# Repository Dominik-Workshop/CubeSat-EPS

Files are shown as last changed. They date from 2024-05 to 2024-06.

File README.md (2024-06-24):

# EPS - Electric Power System

## Used tools:
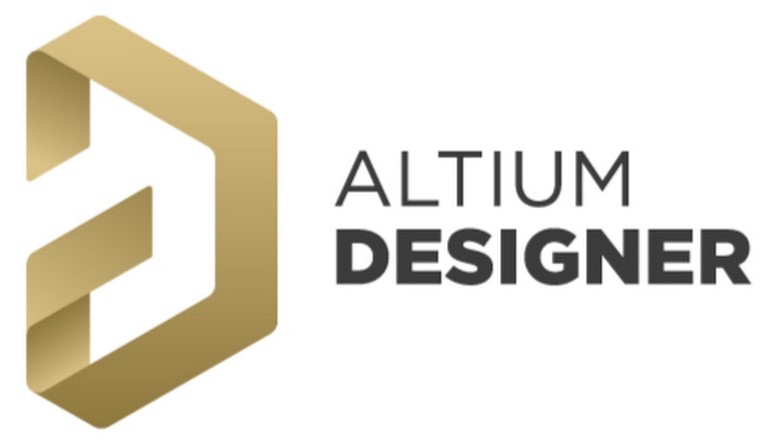
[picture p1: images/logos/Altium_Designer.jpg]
&nbsp;&nbsp;&nbsp;&nbsp; &nbsp;&nbsp;&nbsp;&nbsp; 
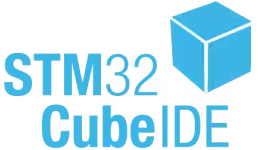
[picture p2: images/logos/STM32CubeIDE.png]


# Project Overview
This project is part of a CubeSat prototype built as a group project at Wrocław University of Science and Technology. [GitLab Repository](https://gitlab.com/wust-satellite)
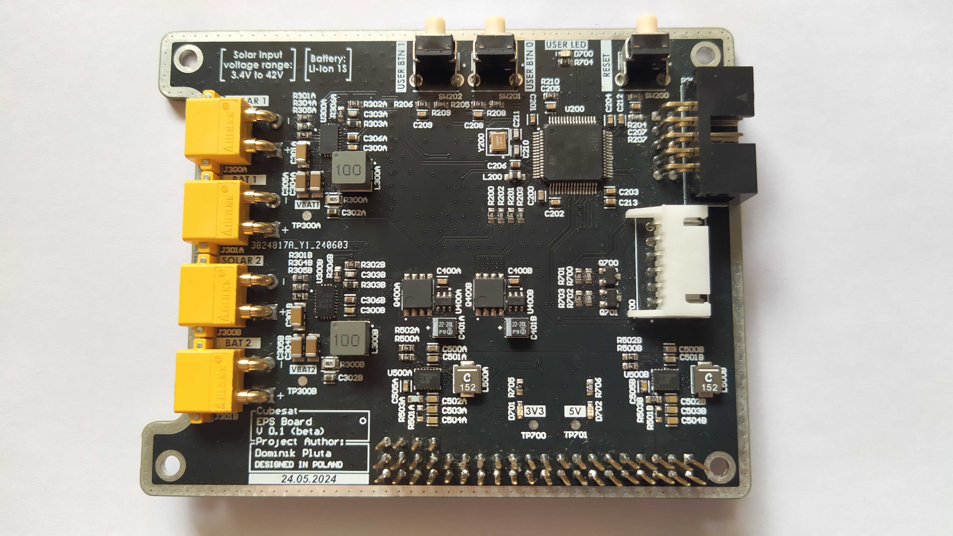
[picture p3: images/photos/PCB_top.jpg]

The primary functions of this board are:

1. **Battery Management**:
    - Charging a 1S Li-ion battery pack using Maximum Power Point Tracking (MPPT).
    - Monitoring the battery voltage.

2. **Power Conversion**:
    - Generating stable 5V and 3.3V power rails to supply various components of the system.

3. **Communication**:
    - Establishing UART communication with a radio board for data transmission and control.

4. **Deployment of Solar Panels and Radio Antenna**:
    - Providing two power outputs capable of driving high current to external resistors, which can burn wires to deploy the solar panels and antenna.

5. **Remove Before Flight (RBF) Circuit**:
    - Ensuring that the satellite starts operation only after ejection from the launch vehicle.

> [!NOTE]
> Certain features, such as current monitoring and switches on all power lines, were omitted due to time constraints.

# Schematic - top sheet
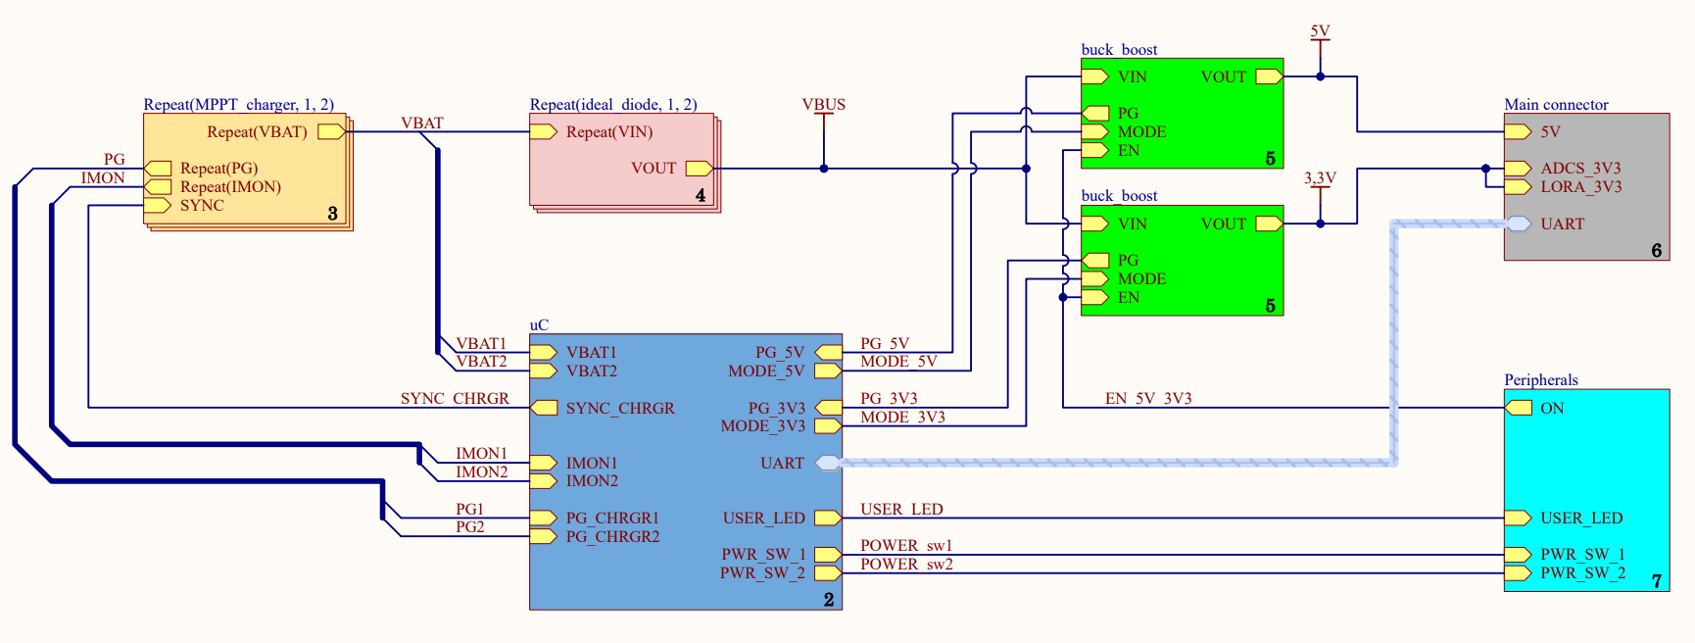
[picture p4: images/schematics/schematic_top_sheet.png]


# PCB
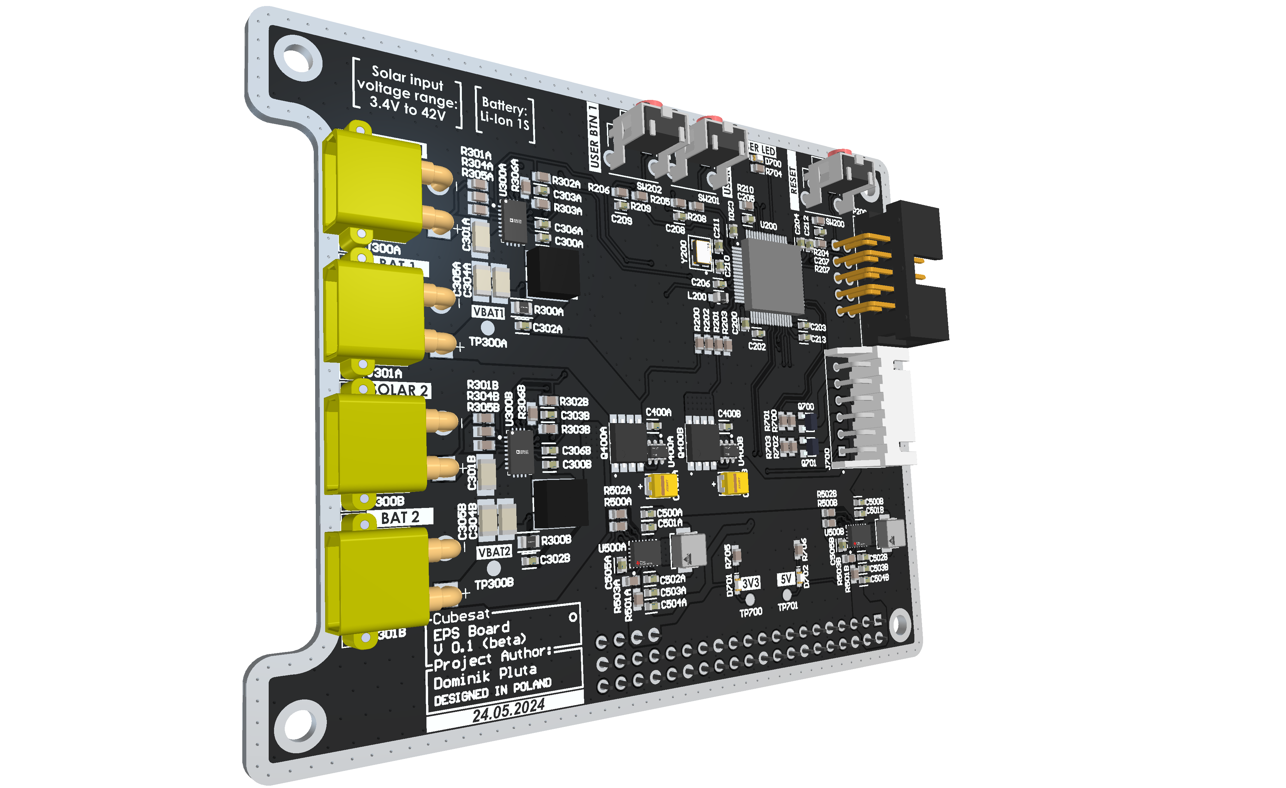
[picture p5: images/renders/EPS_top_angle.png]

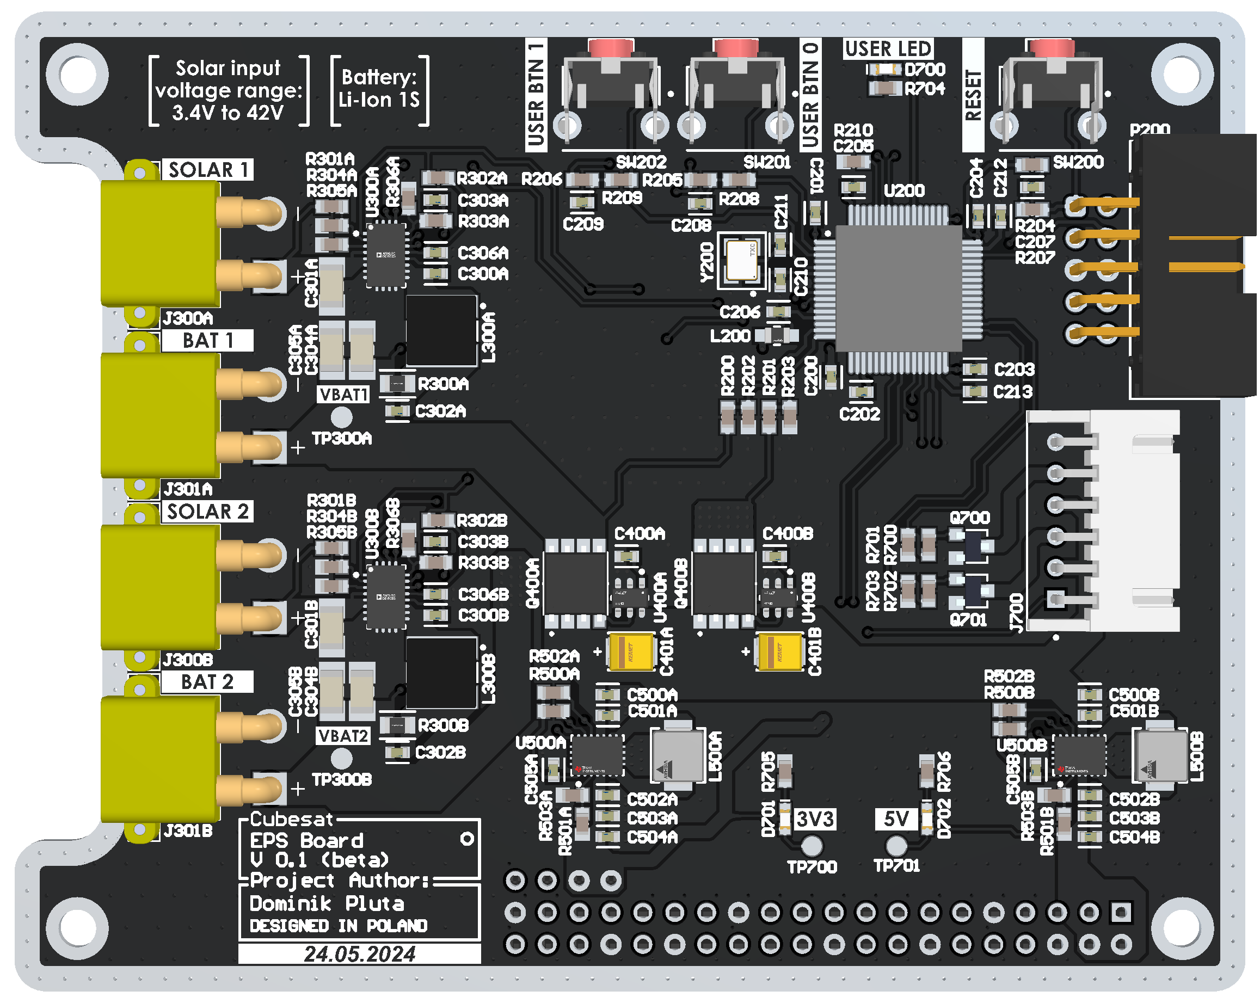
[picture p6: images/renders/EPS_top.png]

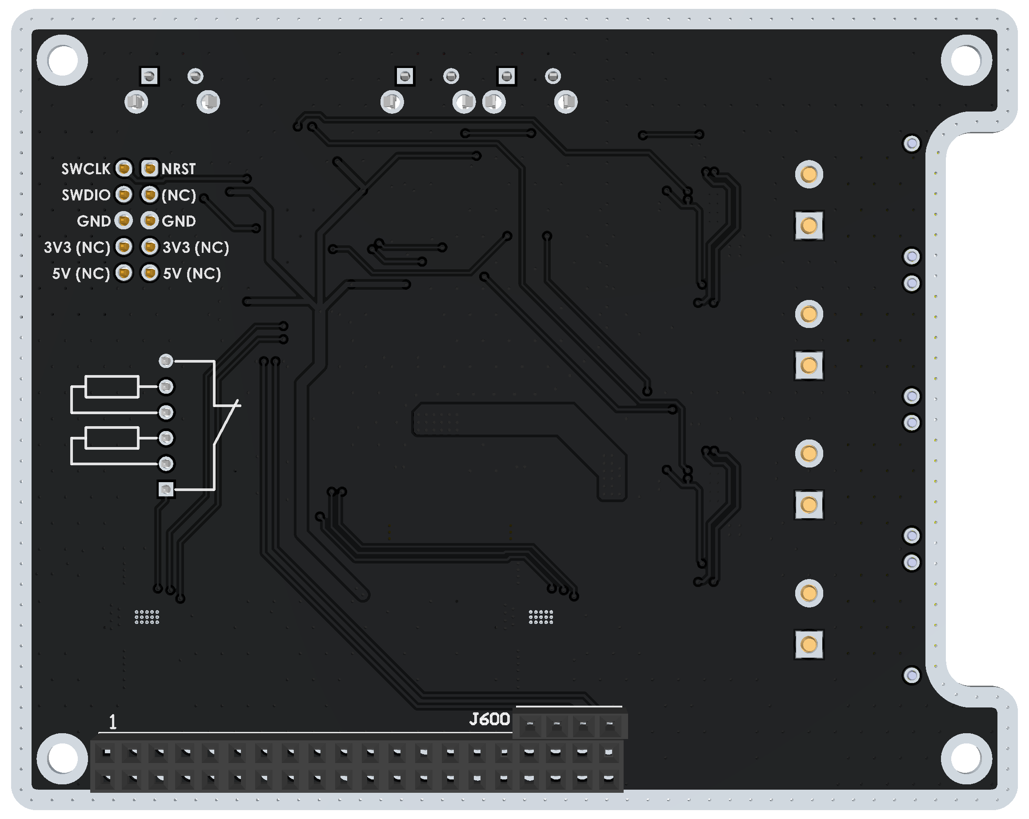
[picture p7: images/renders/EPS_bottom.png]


# Project structure
```
.
├── images
│   ├── logos
│   ├── photos
│   ├── renders
│   └── schematics
├── pcb
│   ├── ***Altium schematic and PCB Documents***
│   ├── ***Altium CAMtastic Documents***
│   ├── ***other Altium files***
│   ├── Lib
│   │   └── ***My parts libraries***
│   └── Project Outputs for EPS_board
│       ├── EPS_full_schematic.pdf
│       ├── ***Gerber and NC drill files***
│       └── EPS_gerber_files.zip
├── code
│   └── ***STM32CubeIDE project***
└── README.md
```

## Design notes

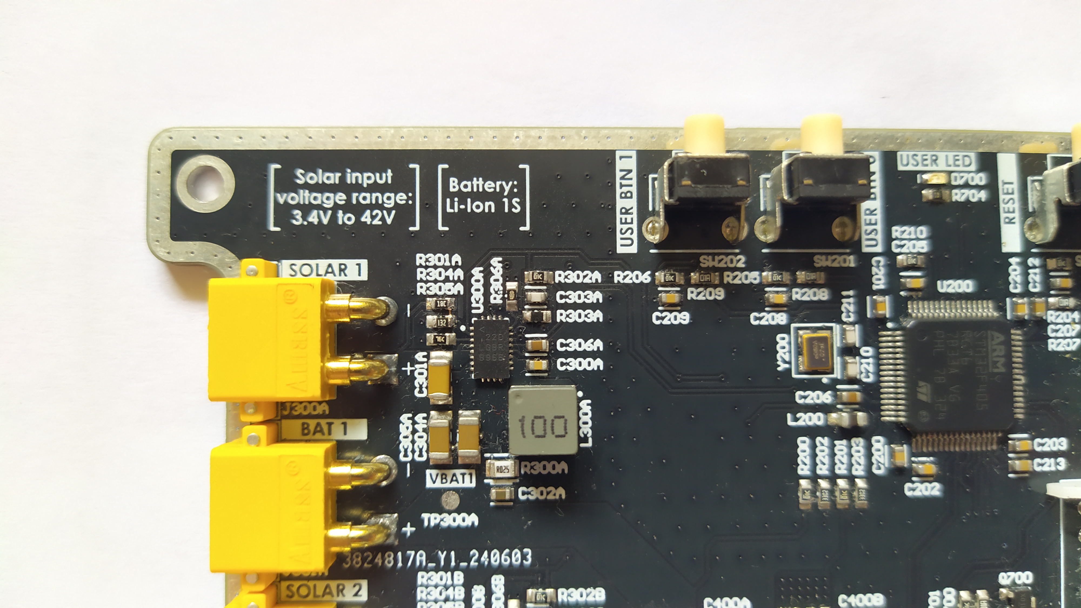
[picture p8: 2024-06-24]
images/photos/PCB_top_closeup2.jpg

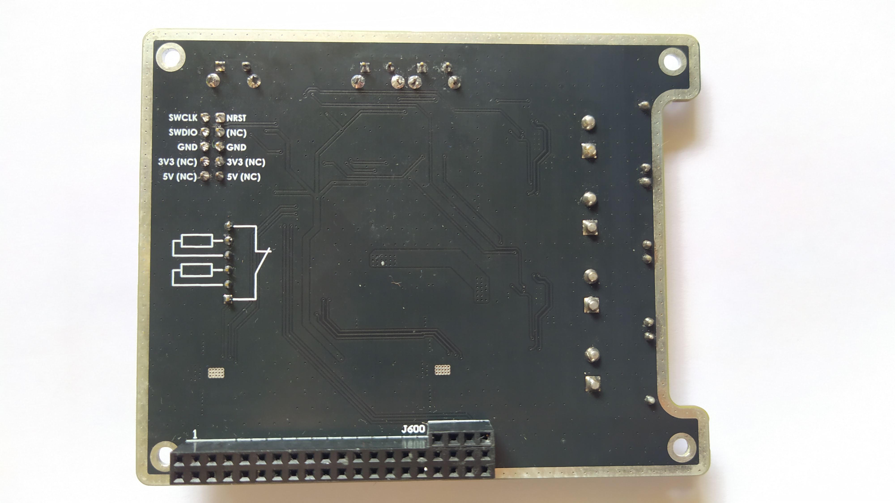
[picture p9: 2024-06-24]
images/photos/PCB_back.jpg

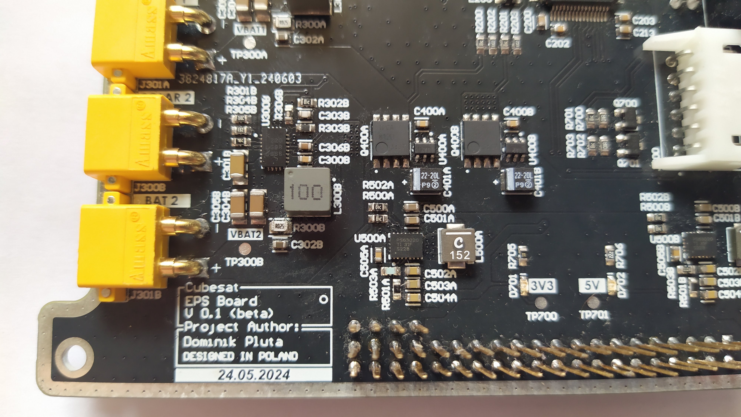
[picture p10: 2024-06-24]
images/photos/PCB_top_closeup1.jpg

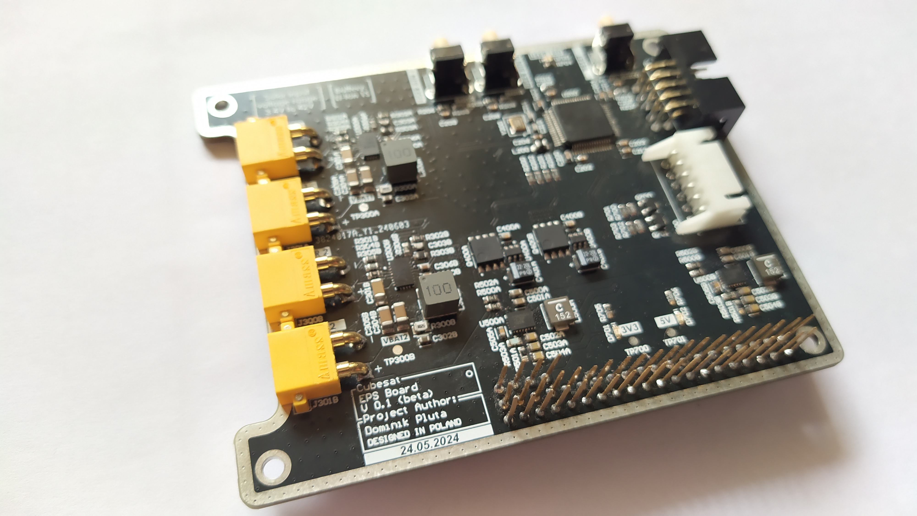
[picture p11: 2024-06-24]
images/photos/PCB_top_angle.jpg

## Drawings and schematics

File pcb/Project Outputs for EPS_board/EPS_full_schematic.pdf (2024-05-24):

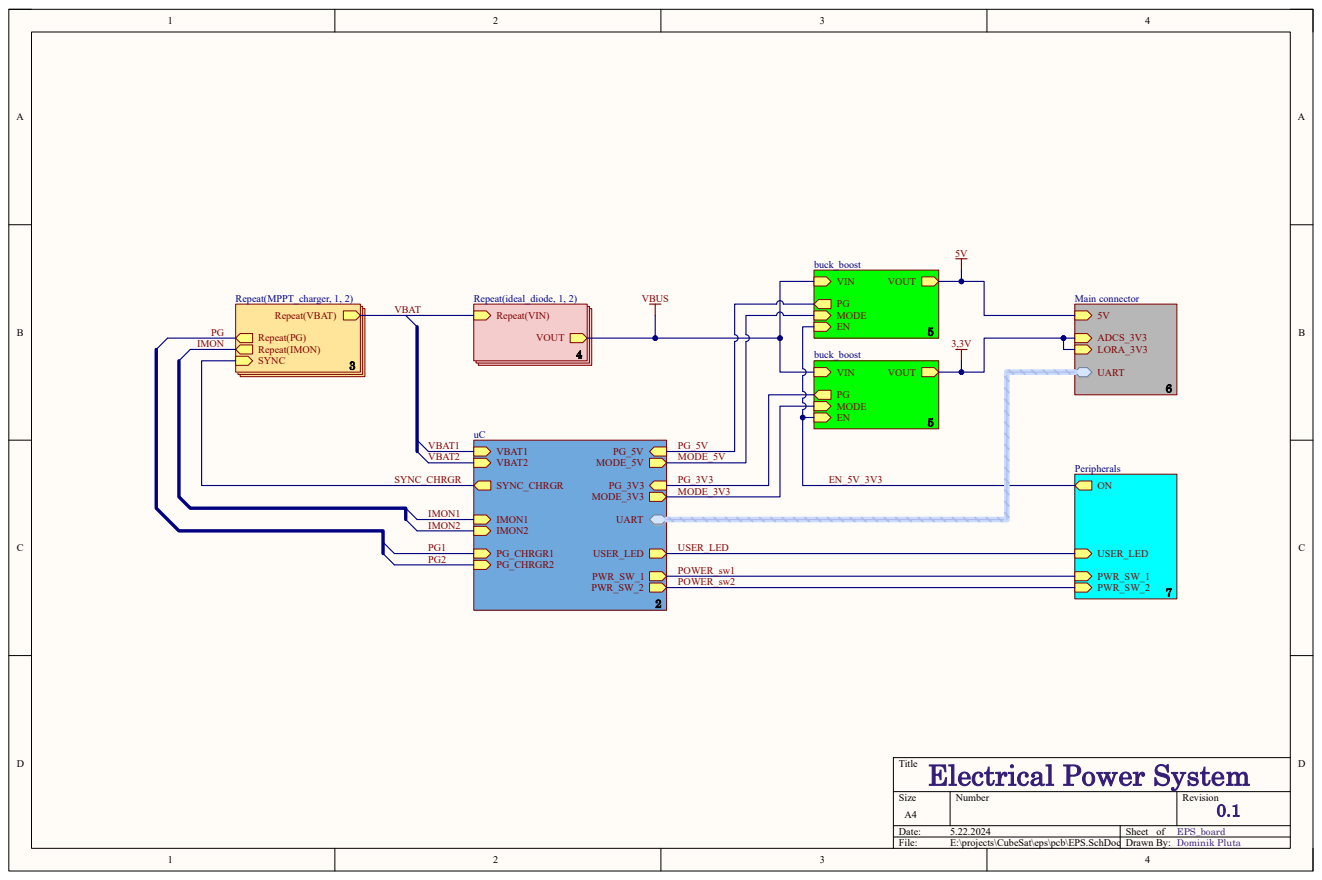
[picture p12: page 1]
Size; Number; Revision; Date:; Sheet of; File:; E:\projects\CubeSat\eps\pcb\EPS.SchDoc; Drawn By:; VBAT1 VBAT2; USER_LED; MODE_5V; MODE_3V3; IMON1; PG_CHRGR1; SYNC_CHRGR; IMON2; PG_CHRGR2; UART; PWR_SW_1 PWR_SW_2; Repeat(PG) Repeat(IMON); Repeat(VBAT); SYNC; Repeat(MPPT_charger, 1, 2); Dominik Pluta; EPS_board; VIN; MODE; VOUT; buck_boost; 3,3V VOUT; Repeat(VIN); Repeat(ideal_diode, 1, 2); VBAT; ADCS_3V3 LORA_3V3; Main connector; Peripherals; VBUS; PG_3V3 MODE_3V3; PG_5V MODE_5V; IMON1 IMON2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

Electrical Power System
Title

# uC power supply Voltage divider

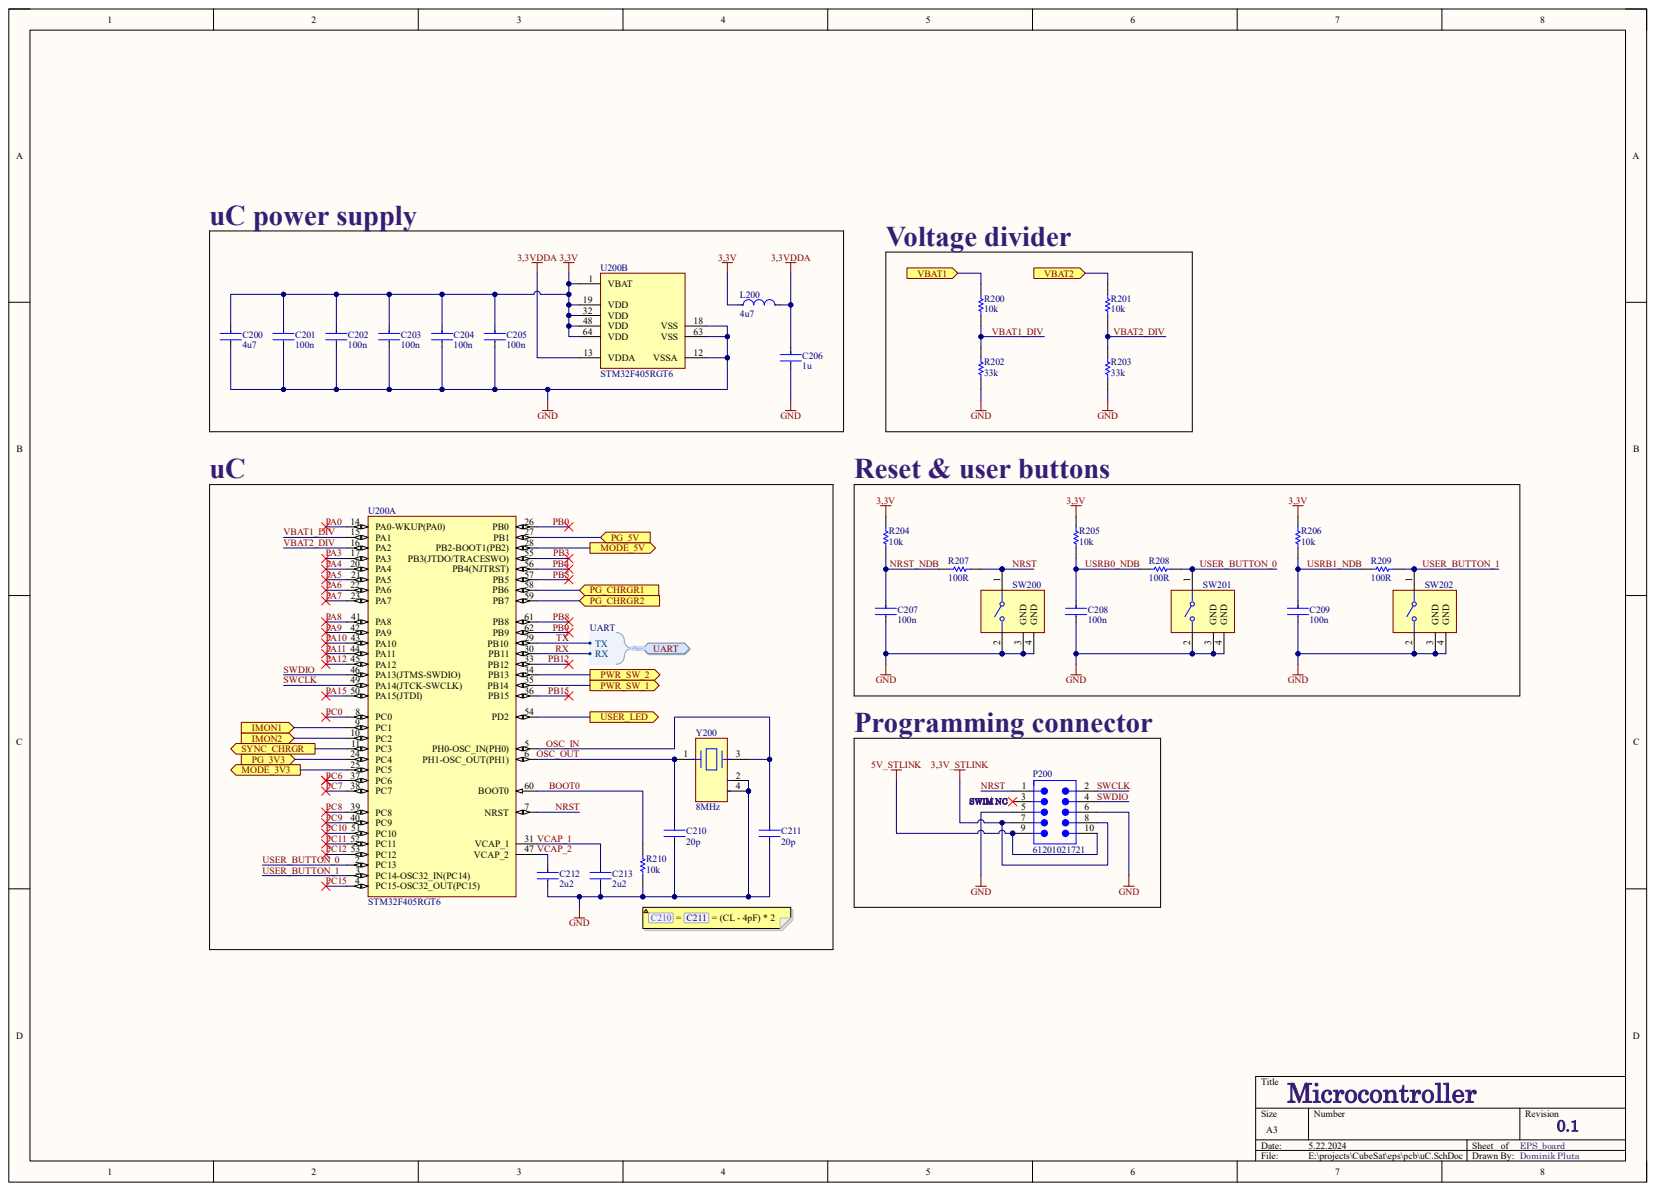
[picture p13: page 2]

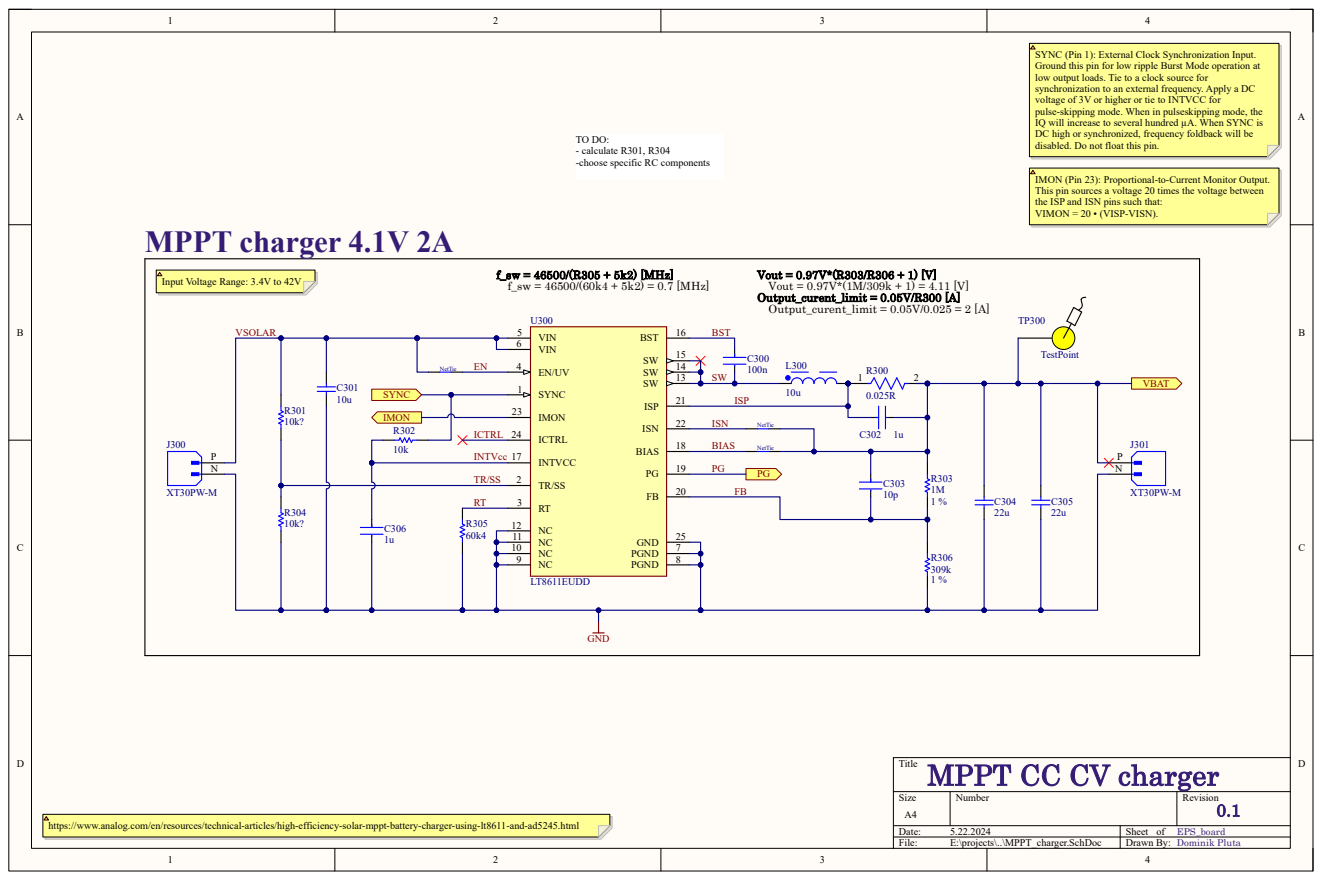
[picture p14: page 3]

SYNC (Pin 1): External Clock Synchronization Input.
Ground this pin for low ripple Burst Mode operation at
low output loads. Tie to a clock source for
synchronization to an external frequency. Apply a DC
voltage of 3V or higher or tie to INTVCC for
pulse-skipping mode. When in pulseskipping mode, the
IQ will increase to several hundred µA. When SYNC is
DC high or synchronized, frequency foldback will be
disabled. Do not float this pin.

- calculate R301, R304
-choose specific RC components

IMON (Pin 23): Proportional-to-Current Monitor Output.
This pin sources a voltage 20 times the voltage between
the ISP and ISN pins such that:
VIMON = 20 • (VISP-VISN).

f_sw = 46500/(60k4 + 5k2) = 0.7 [MHz] Input Voltage Range: 3.4V to 42V

MPPT CC CV charger
Title

https://www.analog.com/en/resources/technical-articles/high-efficiency-solar-mppt-battery-charger-using-lt8611-and-ad5245.html

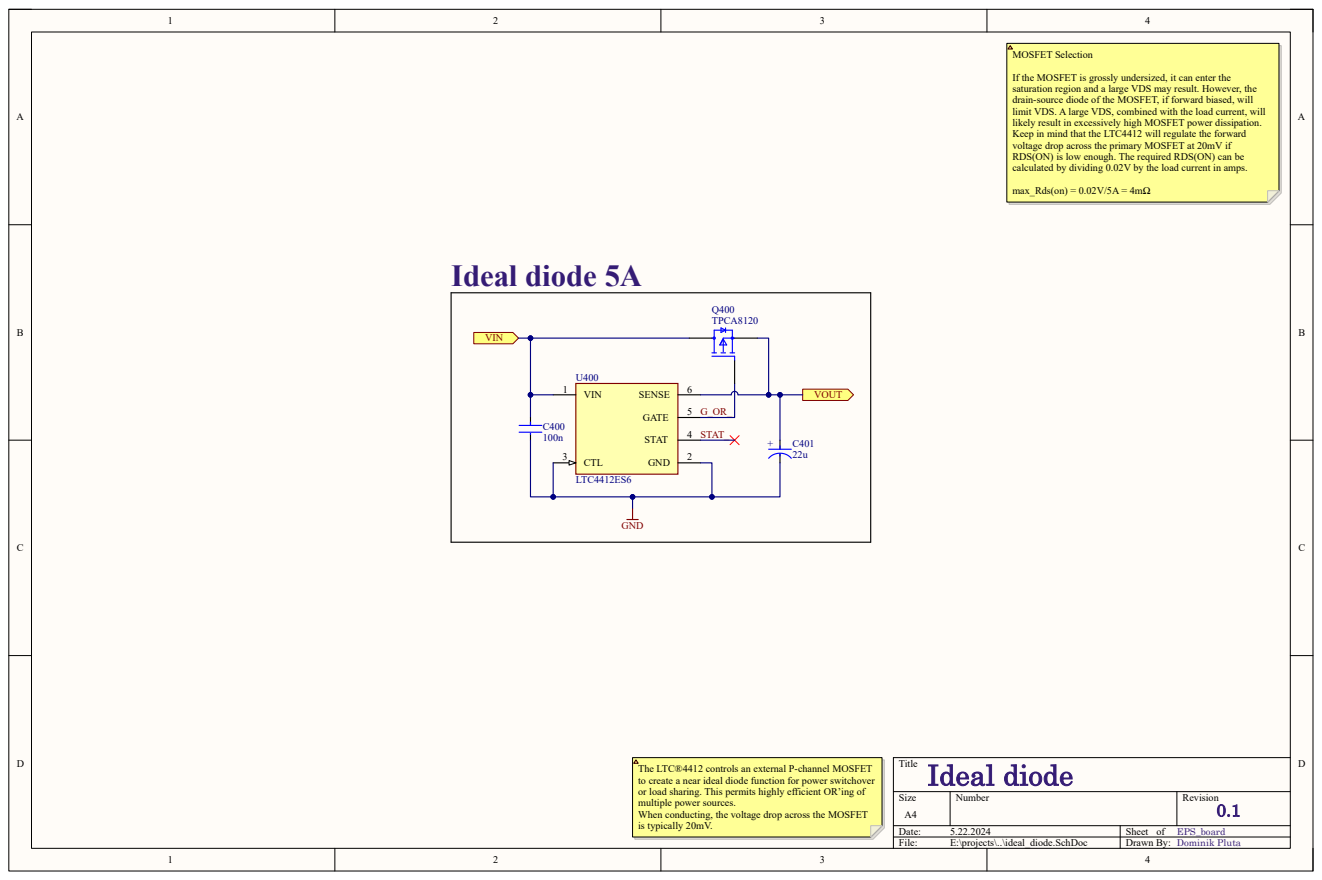
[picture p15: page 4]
Title; Size; Number; Revision; File:; E:\projects\..\ideal_diode.SchDoc; Drawn By:; VOUT; CTL 3; VIN 1; GATE; GND; SENSE; STAT; LTC4412ES6; VIN; STAT_; Ideal diode; Ideal diode 5A; Q400 TPCA8120; MOSFET Selection; max_Rds(on) = 0.02V/5A = 4mΩ

If the MOSFET is grossly undersized, it can enter the
saturation region and a large VDS may result. However, the
drain-source diode of the MOSFET, if forward biased, will
limit VDS. A large VDS, combined with the load current, will
likely result in excessively high MOSFET power dissipation.
Keep in mind that the LTC4412 will regulate the forward
voltage drop across the primary MOSFET at 20mV if
RDS(ON) is low enough. The required RDS(ON) can be
calculated by dividing 0.02V by the load current in amps.

The LTC®4412 controls an external P-channel MOSFET
to create a near ideal diode function for power switchover
or load sharing. This permits highly efficient OR’ing of
multiple power sources.
When conducting, the voltage drop across the MOSFET
is typically 20mV.

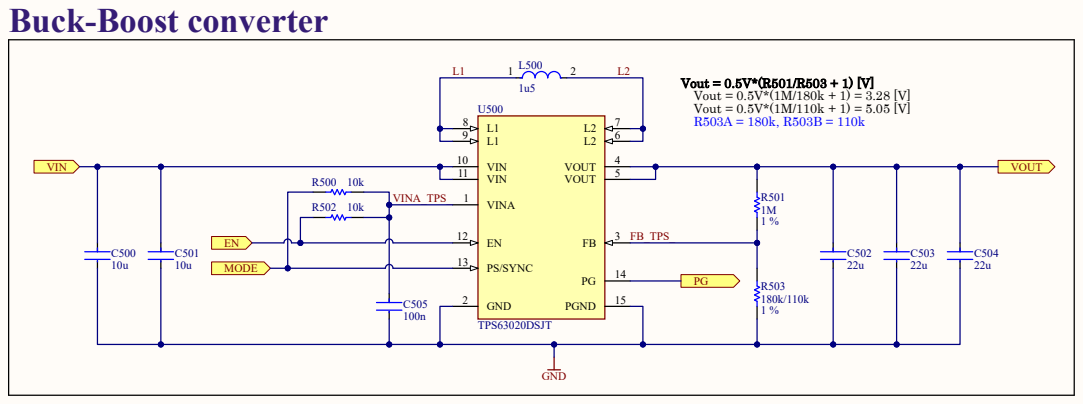
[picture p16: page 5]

PS/SYNC (Pin 13): can be used to select different operation
modes. Power save mode is used to improve efficiency at light
load. To enable power-save, PS/SYNC must be set low. If
PS/SYNC is set low then power save mode is entered when the
average inductor current gets lower then about 100 mA. At this
point the converter operates with reduced switching frequency
and with a minimum quiescent current to maintain high
efficiency.

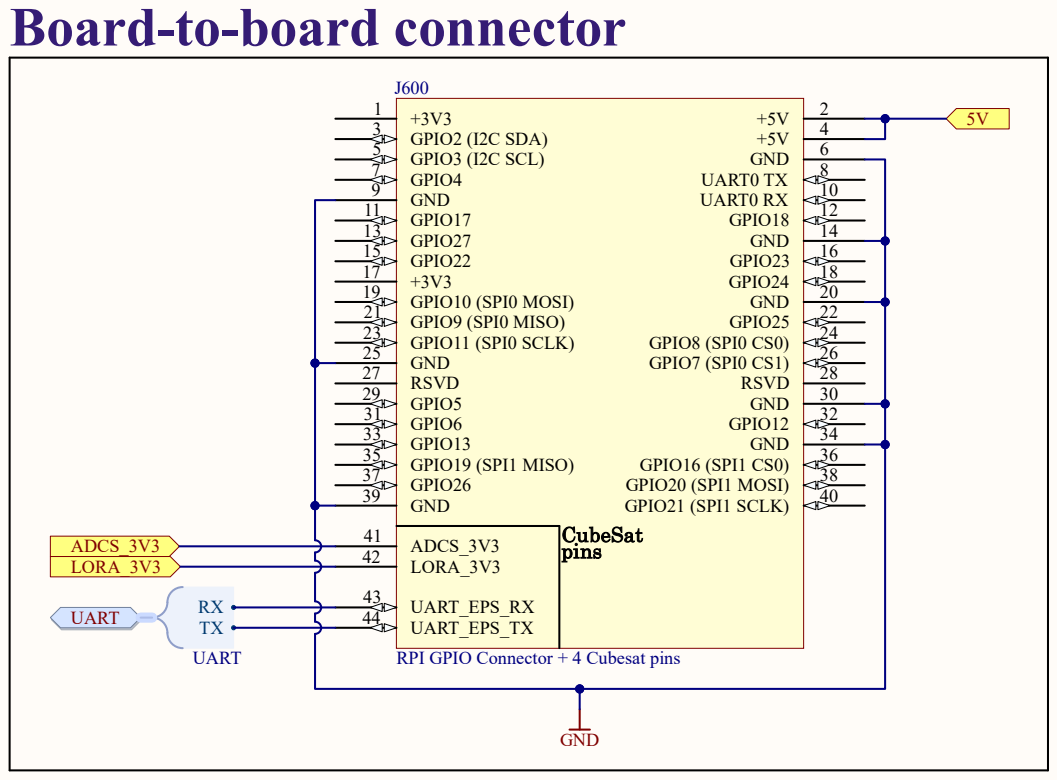
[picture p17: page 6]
Size; Number; Revision; File:; E:\projects\..\main_connector.SchDoc; Drawn By:; GPIO2 (I2C SDA) 3; GPIO3 (I2C SCL) 5; GND; GPIO4 7; UART0 TX; GND 9; UART0 RX; GPIO17 11; GPIO18; GPIO27 13; GPIO22 15; GPIO23; GPIO24; GPIO10 (SPI0 MOSI) 19; GPIO9 (SPI0 MISO) 21; GPIO25; GPIO11 (SPI0 SCLK) 23; GPIO8 (SPI0 CS0); GND 25; GPIO7 (SPI0 CS1); RSVD 27; RSVD; GPIO5 29; GPIO6 31; GPIO12; GPIO13 33; GPIO19 (SPI1 MISO) 35; GPIO16 (SPI1 CS0); GPIO26 37; GPIO20 (SPI1 MOSI); GND 39; GPIO21 (SPI1 SCLK)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

Board-to-board connector

RPI GPIO Connector + 4 Cubesat pins

Title

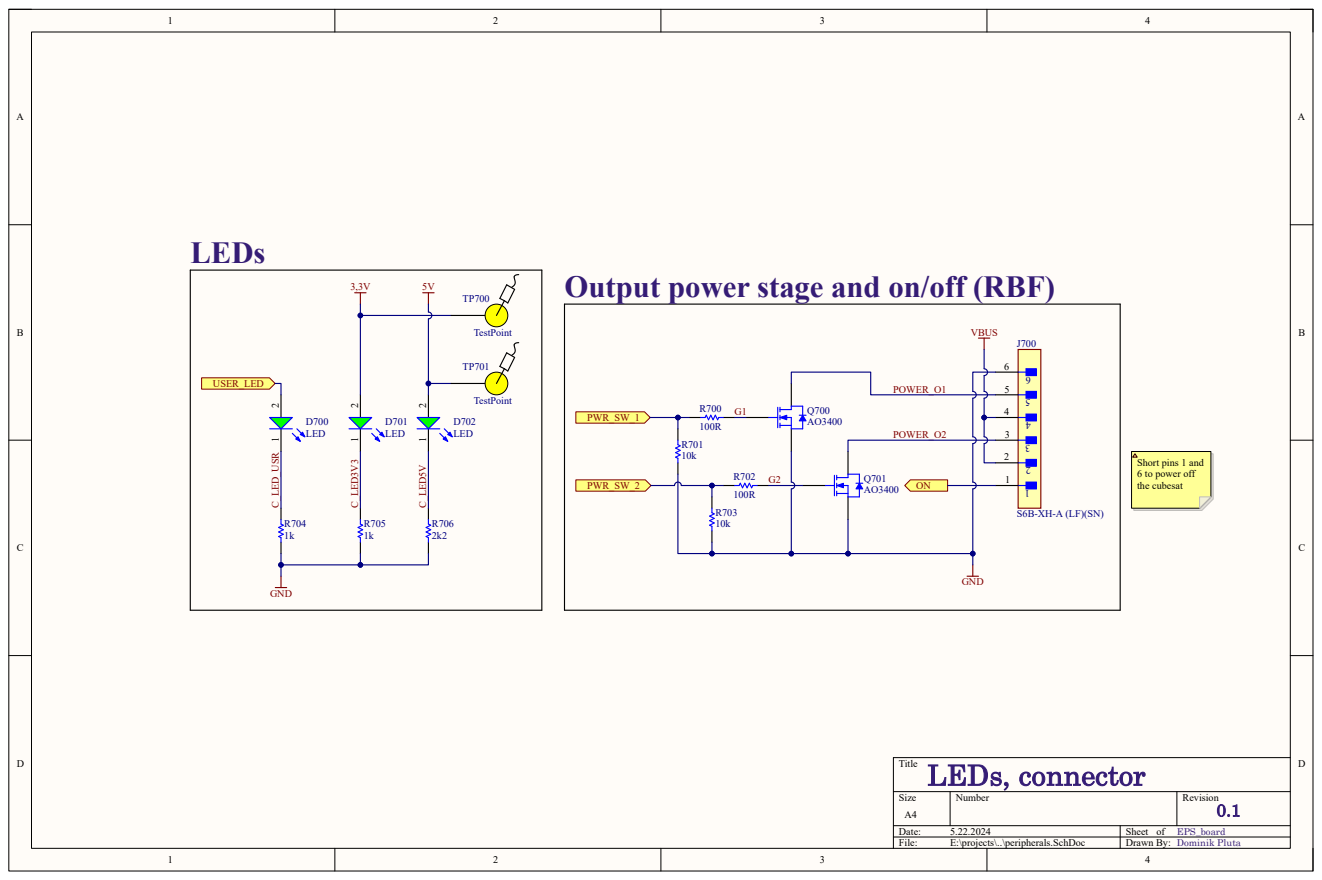
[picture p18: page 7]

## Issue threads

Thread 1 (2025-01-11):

Request: Add information about project status to README

DeflateAwning, 2025-01-11:
Hey, this looks like an awesome project!

I was hoping you could add information about the status of this project. Is it complete? Tested? Still under development? Somewhat on hold?

Dominik-Workshop, 2025-01-11:
Hello! I'm glad you like the project—thank you for your interest!

The EPS was fully tested, and all its functions work as intended. The PCB and code for this board are complete, and I am no longer actively developing it.

We successfully integrated the EPS into our CubeSat, which has been fully built and operates as planned. Other components of the CubeSat were developed by my colleagues, and you can find more details about the entire project in our GitLab repository here: [WUST Satellite Architecture](https://gitlab.com/wust-satellite/architecture).

It's worth mentioning that while I consider this part of the project complete, future students at our university—especially those taking the group project course—may decide to build upon this work or develop new features as part of their contributions.

You're absolutely right about adding information regarding the project's status. I'll make it a priority to create a release on this GitHub repository and include details about the status when I find some free time. Thanks for pointing that out!

DeflateAwning, 2025-01-11:
That's fantastic information, thanks a lot!

Closed 2025-04-16.

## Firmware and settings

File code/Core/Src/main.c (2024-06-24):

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
/* Includes ------------------------------------------------------------------*/
#include "main.h"
#include "adc.h"
#include "dma.h"
#include "usart.h"
#include "gpio.h"

/* USER CODE BEGIN Includes */
#include "stdio.h"
#include "eps.h"
#include "led.h"
/* USER CODE END Includes */


/* USER CODE BEGIN PV */
uint16_t adc_raw_values[4];
EPS eps;

/* USER CODE END PV */

void SystemClock_Config(void);

/* USER CODE BEGIN 0 */
/**
 * @brief function for printing using UART
 */
int _write(int file, char* ptr, int len){
	HAL_UART_Transmit(&huart3, (uint8_t *)ptr, len, HAL_MAX_DELAY);
	return len;
}

/* USER CODE END 0 */

/**
  * @brief  The application entry point.
  * @retval int
  */
int main(void)
{
  /* MCU Configuration--------------------------------------------------------*/

  /* Reset of all peripherals, Initializes the Flash interface and the Systick. */
  HAL_Init();

  /* Configure the system clock */
  SystemClock_Config();

  /* Initialize all configured peripherals */
  MX_GPIO_Init();
  MX_DMA_Init();
  MX_ADC1_Init();
  MX_USART3_UART_Init();
  /* USER CODE BEGIN 2 */
  HAL_ADC_Start_DMA(&hadc1, adc_raw_values, 4);
  setLedPattern(&(eps.led), LED_BLINK_SLOW);  // Example pattern

  eps.powerStatus = 0x00;
  /* USER CODE END 2 */

  /* Infinite loop */
  /* USER CODE BEGIN WHILE */
  HAL_Delay(10000);
  deploySolarPanels();
  HAL_Delay(5000);
  deployAntenna();
  while (1){
	  eps.battery1.adcRawVoltageReading = adc_raw_values[0];
	  eps.battery2.adcRawVoltageReading = adc_raw_values[1];
	  eps.battery1.adcRawCurrentReading = adc_raw_values[2];
	  eps.battery2.adcRawCurrentReading = adc_raw_values[3];

	  calculateBatteryVoltage(&(eps.battery1));
	  calculateBatteryVoltage(&(eps.battery2));
	  calculateBatteryChargingCurrent(&(eps.battery1));
	  calculateBatteryChargingCurrent(&(eps.battery2));

	  eps.powerStatus = checkPowerGoodSignals(&(eps.powerGoodSignals));
	  handlePowerGoodErrors(&eps);

	  if(!HAL_GPIO_ReadPin(USER_BUTTON_0_GPIO_Port, USER_BUTTON_0_Pin)){
		  deploySolarPanels();
		  setLedPattern(&(eps.led), LED_BLINK_FAST);
	  }
	  if(!HAL_GPIO_ReadPin(USER_BUTTON_1_GPIO_Port, USER_BUTTON_1_Pin)){
		  deployAntenna();
		  setLedPattern(&(eps.led), LED_BLINK_BURST);
	  }
	  printf("%d; %d; %d; %d; %d \n\r", eps.battery1.voltage_mV, eps.battery2.voltage_mV, eps.battery1.chargingCurrent_mA, eps.battery2.chargingCurrent_mA, eps.powerStatus);
	  updateLed(&(eps.led));
	  HAL_Delay(10);
    /* USER CODE END WHILE */

    /* USER CODE BEGIN 3 */
  }
  /* USER CODE END 3 */
}

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


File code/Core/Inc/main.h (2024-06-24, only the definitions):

#define USER_BUTTON_0_Pin GPIO_PIN_13
#define USER_BUTTON_0_GPIO_Port GPIOC
#define USER_BUTTON_1_Pin GPIO_PIN_14
#define USER_BUTTON_1_GPIO_Port GPIOC
#define CHARGER1_IMON_Pin GPIO_PIN_1
#define CHARGER1_IMON_GPIO_Port GPIOC
#define CHARGER2_IMON_Pin GPIO_PIN_2
#define CHARGER2_IMON_GPIO_Port GPIOC
#define CHARGER_SYNC_Pin GPIO_PIN_3
#define CHARGER_SYNC_GPIO_Port GPIOC
#define BATTERY1_VOLTAGE_Pin GPIO_PIN_1
#define BATTERY1_VOLTAGE_GPIO_Port GPIOA
#define BATTERY2_VOLTAGE_Pin GPIO_PIN_2
#define BATTERY2_VOLTAGE_GPIO_Port GPIOA
#define POWER_GOOD_3V3_Pin GPIO_PIN_4
#define POWER_GOOD_3V3_GPIO_Port GPIOC
#define MODE_3V3_Pin GPIO_PIN_5
#define MODE_3V3_GPIO_Port GPIOC
#define POWER_GOOD_5V_Pin GPIO_PIN_1
#define POWER_GOOD_5V_GPIO_Port GPIOB
#define MODE_5V_Pin GPIO_PIN_2
#define MODE_5V_GPIO_Port GPIOB
#define POWER_SWITCH2_Pin GPIO_PIN_13
#define POWER_SWITCH2_GPIO_Port GPIOB
#define POWER_SWITCH1_Pin GPIO_PIN_14
#define POWER_SWITCH1_GPIO_Port GPIOB
#define USER_LED_Pin GPIO_PIN_2
#define USER_LED_GPIO_Port GPIOD
#define POWER_GOOD_CHARGER1_Pin GPIO_PIN_6
#define POWER_GOOD_CHARGER1_GPIO_Port GPIOB
#define POWER_GOOD_CHARGER2_Pin GPIO_PIN_7
#define POWER_GOOD_CHARGER2_GPIO_Port GPIOB

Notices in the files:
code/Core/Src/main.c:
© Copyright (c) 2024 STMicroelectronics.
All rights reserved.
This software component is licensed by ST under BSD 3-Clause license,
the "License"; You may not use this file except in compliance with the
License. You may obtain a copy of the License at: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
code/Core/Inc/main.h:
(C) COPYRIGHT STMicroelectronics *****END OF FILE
